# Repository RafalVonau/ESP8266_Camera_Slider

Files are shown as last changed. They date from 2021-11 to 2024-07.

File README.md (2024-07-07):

# Camera slider on ESP8266

## Info

This repository contains the software for my ESP8266 based Camera slider.

Features:
- No collision-detection!!
- WWW page interface ( http://slider.local ),
- Simple commands over TCP (port 2500),
   from linux:
      netcat slider.local 2500
- Simple commands over HTTP POST ( http://slider.local/post ),
- Set mottor current and microsteps per step by a command (software),
- Optional endstop switch for homing.

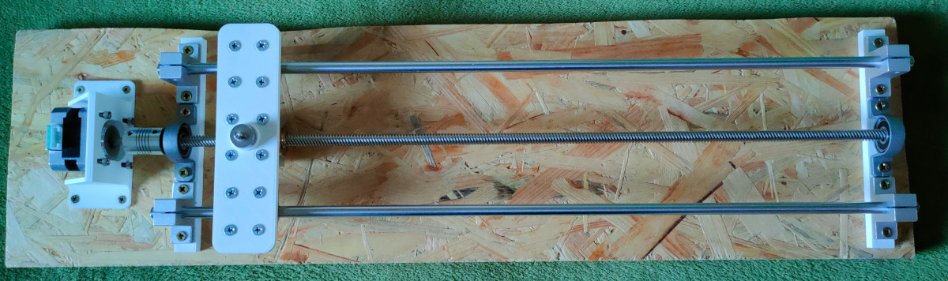
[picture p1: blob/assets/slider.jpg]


# Mechanical parts needed:
* 3D printed pars,
* 1 x T8 Trapezoidal Lead Screw L=500mm,
* 1 x T8 Brass Nut,
* 2 x KP08 Bore Ball Bearing Pillow Block Mounted Support 8mm,
* 2 x 8mm Inner Dia L=34.5mm SCS8UU Linear Bearing,
* 2 x Aluminum 8mm Innner Dia 42x32x11mm SK8 Linear Rod Rail Support Guide Shaft Bearing
* 2 x Linear Shaft Optical Axis 8mm L=500mm,
* 4 x SK8 Linear Rod Rail Shaft,
* 1 x T8 Nut Conversion Seat,
* screws

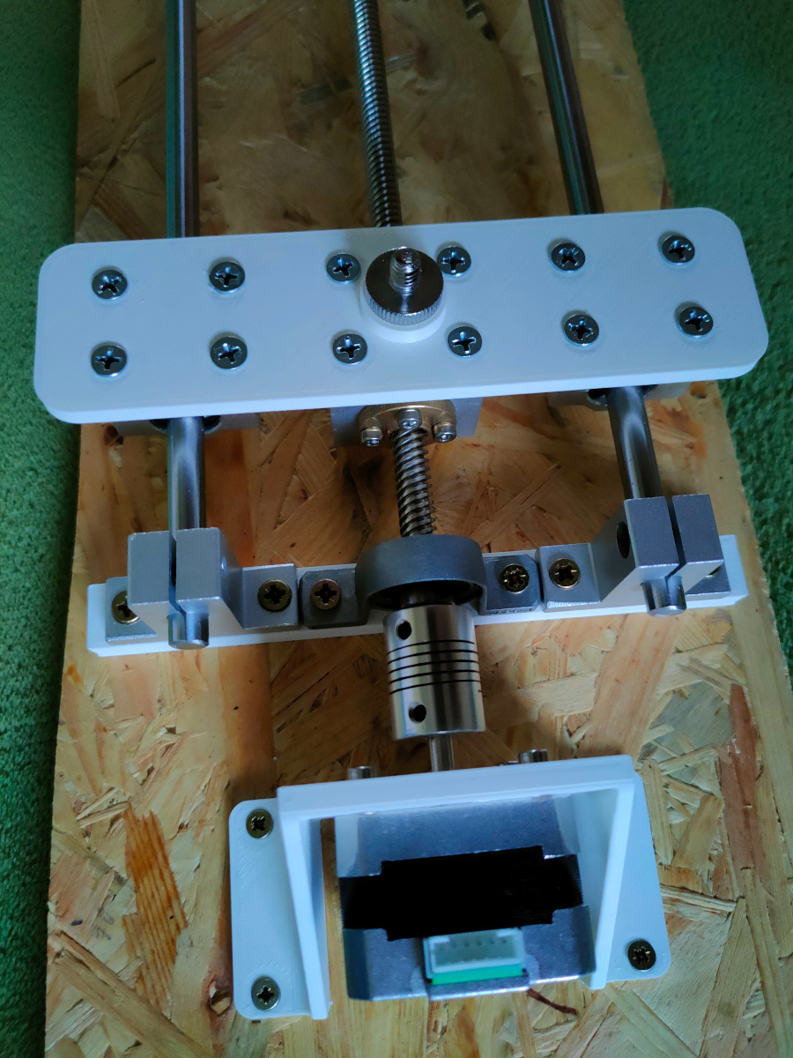
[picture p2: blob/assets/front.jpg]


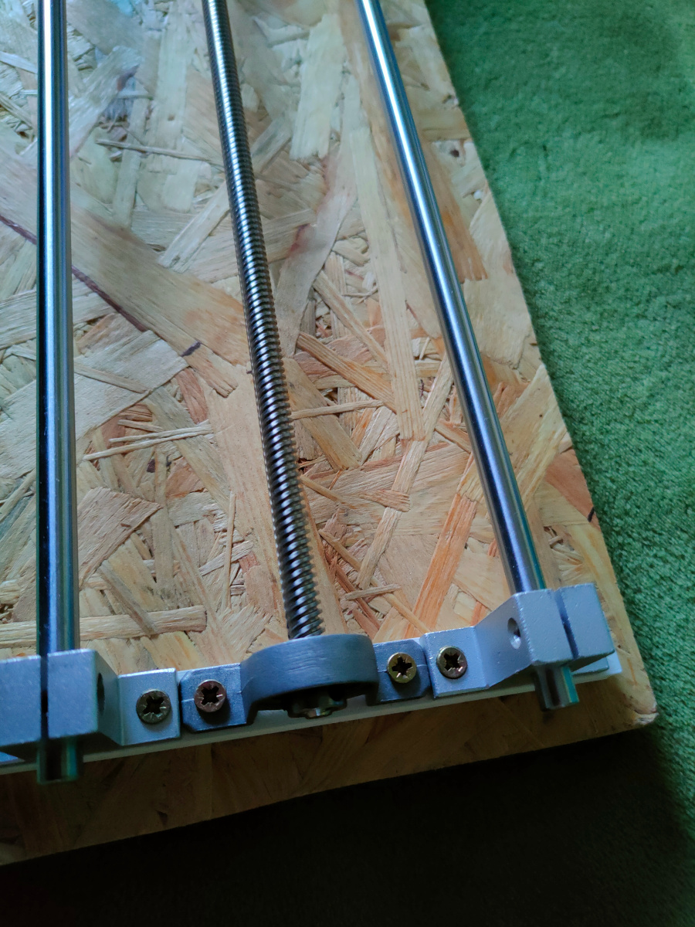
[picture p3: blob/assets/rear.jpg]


# Electrical parts needed:
* ESP8266 (bare ESP8266 module or D1 mini),
* DC/DC converter 12V to 3.3V,
* 1 x TMC2208,
* 1 x Stepper motor Nema 17,
* wires,
* connectors,
* [1 x Limit Switch Endstop for Creality CR-10 10S Ender 3] - OPTIONAL

# D1 mini CONNECTIONS
* STEP      - GPIO14 (D5)
* DIR1      - GPIO13 (D7)
* MOTTOR EN - GPIO2  (D4)
* RX        - TMC2208 single wire UART (1kohm from RX to TX)
* TX        - TMC2208 single wire UART (1kohm from RX to TX)
* ENDSTOP   - GPIO4  (D2)  - OPTIONAL
# Wiring

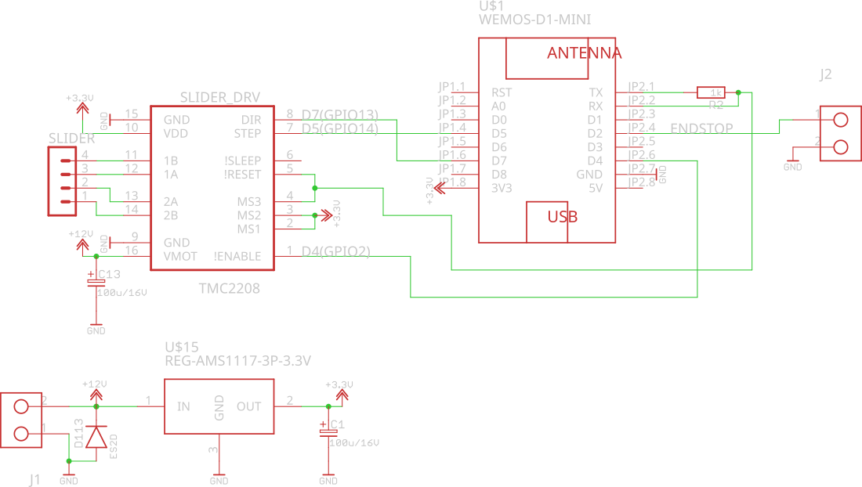
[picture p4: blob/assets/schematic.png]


# Software architecture

The ESP8266 generates STEP and DIR signals to the TMC2208 chip for motor movement. The UART connection allows you to program the TMC2208 chip registers so you can easily change the current and the number of micro steps per step without having to turn a potentiometer or change jumpers. 

STEP signal is generated using Timer1 (for performance reasons the interrupt control was taken from this timer and it was set to AUTORELOAD mode) and because Timer1 is used in servo/pwm(analogWrite)/tone/waveform functions these functions can't be used in this code. 

Commands are received on the fly from TCP channels (port 2500) and the WWW page (POST) and then passed to the command queue. The movement commands are passed to a separate queue so that sequences of movements can be queued. When the move is completed, the next command from the move queue is taken, and so on.

# Building

Uncomment and modify Wifi client settings in secrets.h file:
* #define WIFI_SSID                "Slider"
* #define WIFI_PASS                "SliderPass"

The project uses platformio build environment. 
[PlatformIO](https://platformio.org/) - Professional collaborative platform for embedded development.

* install PlatformIO
* enter project directory
* connect ESP8266 to PC computer over USB to serial cable.
* type in terminal:
  platformio run -t upload

You can also use IDE to build this project on Linux/Windows/Mac. My fvorite ones:
* [Code](https://code.visualstudio.com/) 
* [Atom](https://atom.io/)

# Commands
EM  - enable mottors,

Movement in revolutions:\
M   - absolute move in motor revolutions (M,duration [ms],start_rev,target_rev),\
MR  - relative move in motor revolutions (MR,duration [ms],delta rev),\
MH  - move to home (endstop switch is required),

Movement in microsteps:\
GT  - absolute move in microsteps (GT,duration [ms],start_microstep,target_microstep)\
GTR - relative move in microsteps (GTR,duration [ms],delta microsteps)\
GTH - move to home (endstop switch is required),\
UM  - unconditional relative move in microsteps WARNING: do not check limits. (UM,duration [ms],delta microsteps)

STP - STOP move,

Parameters set:\
G90 - Set this possition as zero point,\
C   - set motor current in [mA],\
S   - set microsteps per step,

STATUS:\
XX  - print status,

Examples:

set mottor curent to 400mA:

C,400

Set 32 misrosteps per step:

S,32

Move from revolution 1 to 45 in 30000 miliseconds:

M,30000,1,45

Move 1 revolution in backward direction in 2 seconds:

MR,2000,1

Stop move:

STP

Enjoy :-)

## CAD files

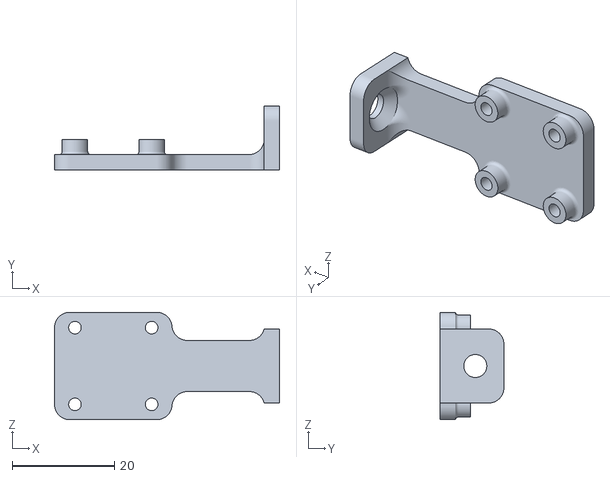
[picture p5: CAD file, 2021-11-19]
PartsTo3DPrint/slider_endstop.stl
44.0 x 12.5 x 21.0

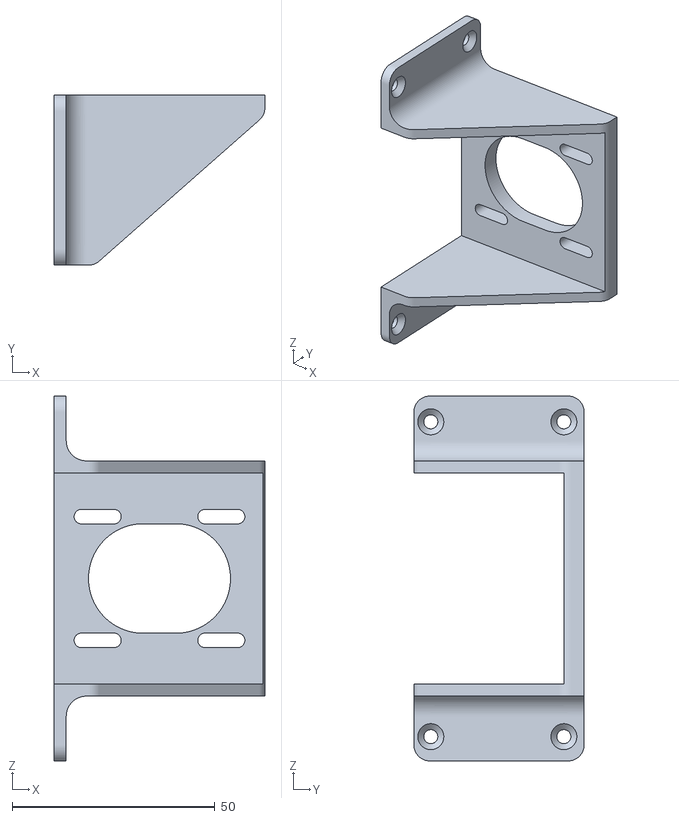
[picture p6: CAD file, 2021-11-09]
PartsTo3DPrint/slider_motor.stl
52.0 x 42.0 x 90.0

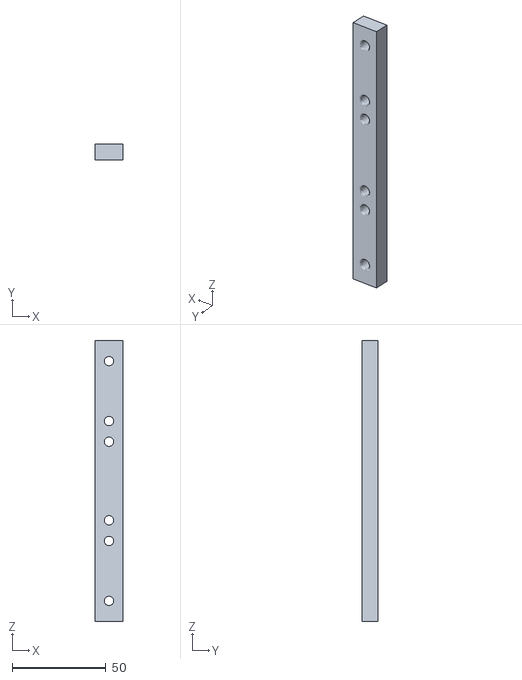
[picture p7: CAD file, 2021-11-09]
PartsTo3DPrint/slider_spacer.stl
15.0 x 8.50 x 150.0

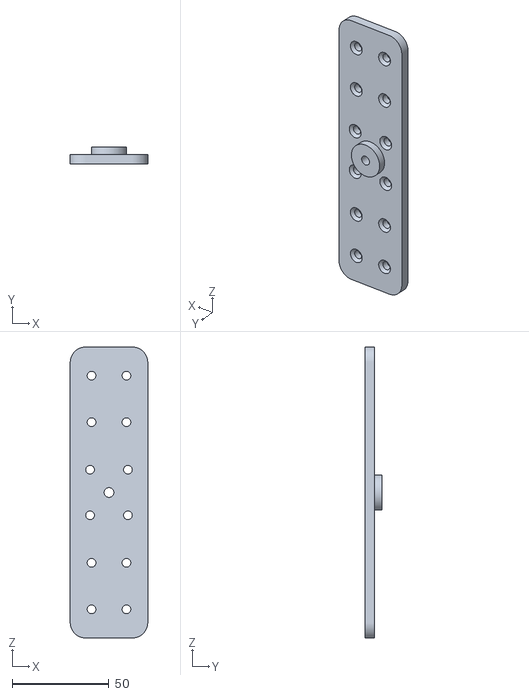
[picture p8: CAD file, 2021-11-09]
PartsTo3DPrint/slider_holder.stl
40.0 x 9.00 x 150.0

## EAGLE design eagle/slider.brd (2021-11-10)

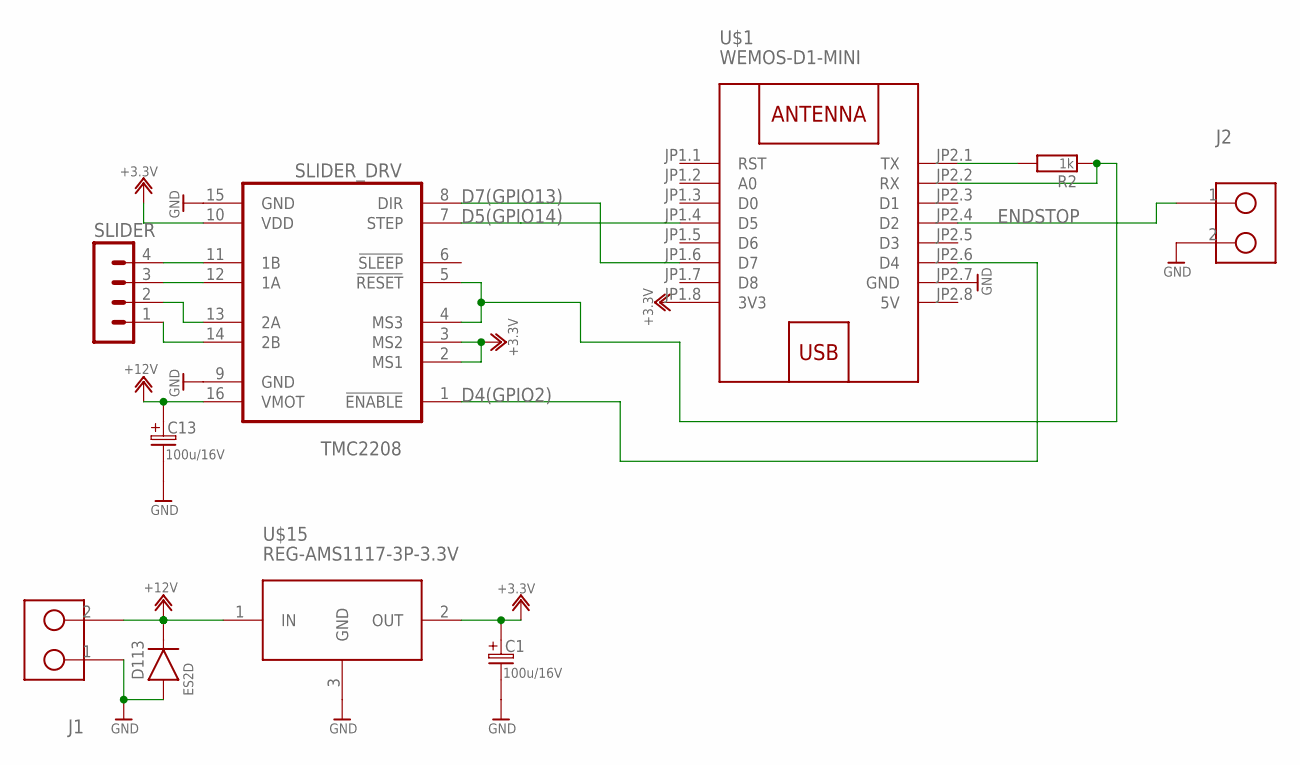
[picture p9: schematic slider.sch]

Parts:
C1, C13: 100u/16V; ES-3,5/8
D113: ES2D; SMB
J1, J2: GMKDS-2; GMKDS1,5
R2: 1k; 0805
SLIDER: MA04-1
SLIDER_DRV: TMC2208; POLOLULU2128
U$1: WEMOS-D1-MINI
U$15: REG-AMS1117-3P-3.3V; REG-AMS1117-3P

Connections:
5V: U$1.JP2.8 (5V)
+3.3V: C1.1, SLIDER_DRV.2 (MS1), SLIDER_DRV.3 (MS2), SLIDER_DRV.10 (VDD), U$1.JP1.8 (3V3), U$15.2 (OUT)
+12V: C13.1, D113.2 (K), J1.2, SLIDER_DRV.16 (VMOT), U$15.1 (IN)
D4(GPIO2): SLIDER_DRV.1 (!ENABLE), U$1.JP2.6 (D4)
D5(GPIO14): SLIDER_DRV.7 (STEP), U$1.JP1.4 (D5)
D7(GPIO13): SLIDER_DRV.8 (DIR), U$1.JP1.6 (D7)
ENDSTOP: J2.1, U$1.JP2.4 (D2)
GND: C1.2, C13.2, D113.1 (A), J1.1, J2.2, SLIDER_DRV.9 (GND), SLIDER_DRV.15 (GND), U$1.JP2.7 (GND), U$15.3 (GND)
unnamed: R2.2, U$1.JP2.1 (TX)
unnamed: R2.1, SLIDER_DRV.4 (MS3), SLIDER_DRV.5 (!RESET), U$1.JP2.2 (RX)
unnamed: SLIDER.4, SLIDER_DRV.11 (1B)
unnamed: SLIDER.3, SLIDER_DRV.12 (1A)
unnamed: SLIDER.2, SLIDER_DRV.13 (2A)
unnamed: SLIDER.1, SLIDER_DRV.14 (2B)

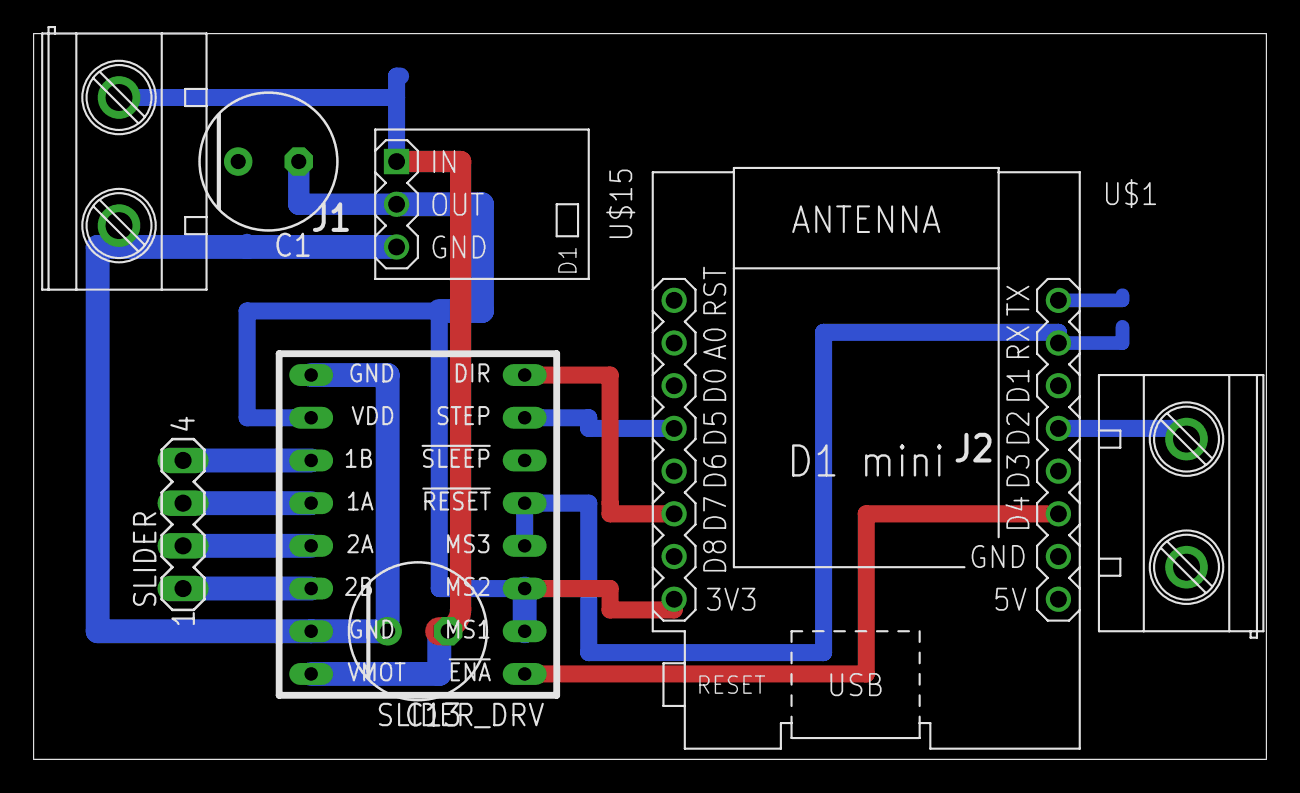
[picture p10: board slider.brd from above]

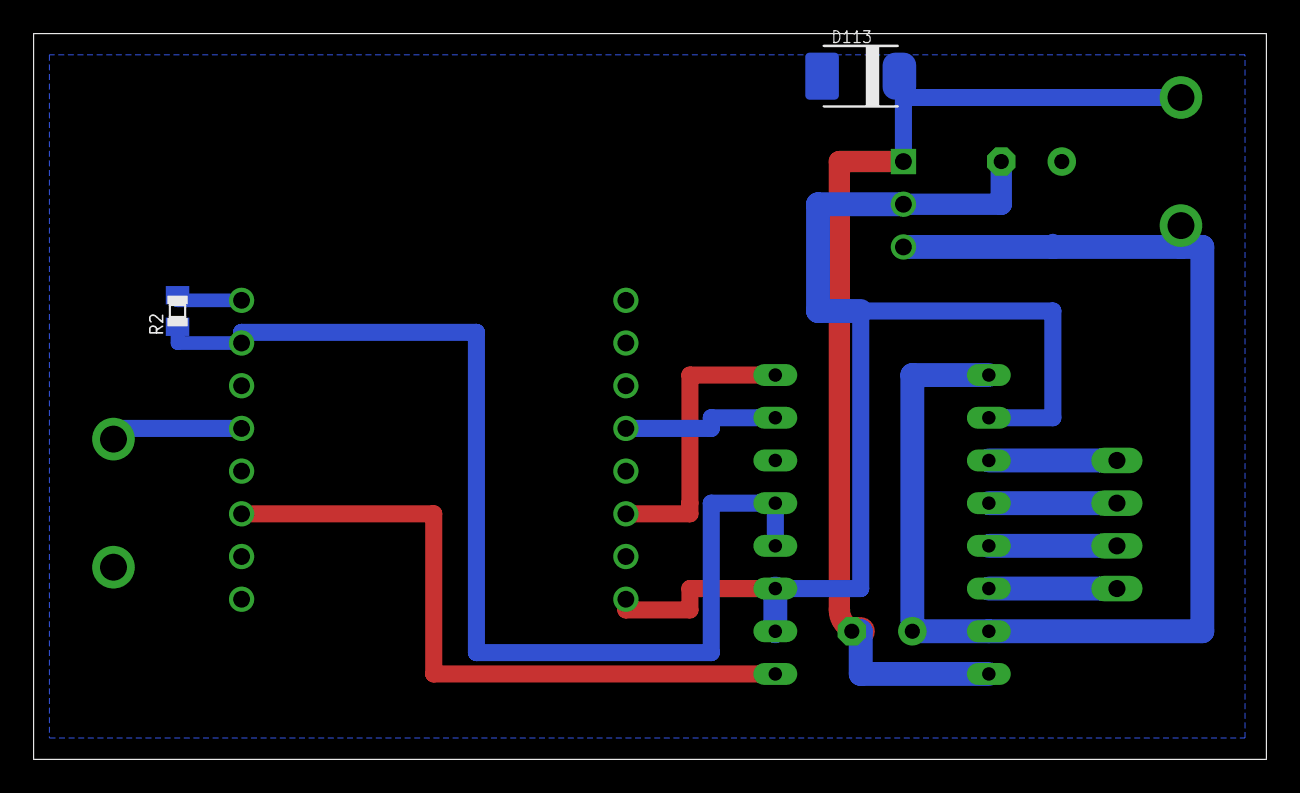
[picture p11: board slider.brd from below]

Board: 2 copper layers, 73.3 x 43.2 mm, 10 parts (2 on the bottom side), 13 nets.

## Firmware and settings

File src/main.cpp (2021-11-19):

#include <ESP8266WiFi.h>
extern "C" {
	#include <osapi.h>
	#include <os_type.h>
}
#include <ArduinoOTA.h>
#include <DNSServer.h>
#include "Motion1D.h"
#include <TMCStepper.h>
#include "NetworkCommand.h"
#include "HTTPCommand.h"
#include "UdpLogger.h"

/* SWITCHES */
#define HOSTNAME                 "slider"
#define NPORT                    (2500)

#define MAX_DIST_MOTTOR (45)

// PIN definition
#define step1        14
#define dir1         13
#define enableMotor  2
#define z_endstop    4


#define SERIAL_PORT Serial    // TMC2208/TMC2224 HardwareSerial port
#define R_SENSE     0.11      // SilentStepStick series use 0.11     Watterott TMC5160 uses 0.075


#ifdef DEBUG_ENABLED
UdpLoggerClass     UdpLogger;
#endif
DNSServer          dnsServer;
class WiFiManager {
	public:
	WiFiManager() {}
	void autoConnect(String x) {
		WiFi.softAP("SliderAP");
		dnsServer.start(53, "*", WiFi.softAPIP());
	}
};
#include "secrets.h"

/* Global variables */
TMC2208Stepper driver = TMC2208Stepper(&SERIAL_PORT, R_SENSE); // Hardware Serial0
Motion1D          *m1d;
CommandDB         CmdDB;
NetworkCommand    *NCmd;
HTTPCommand       *HCmd;
volatile int ota_in_progress = 0;
static int current_microsteps = 256;

static void makeCmdInterface();

/*!
 * \brief Setup.
 * 1. Configure gpio.
 * 2. Connect to WiFi.
 * 3. Setup OTA.
 * 4. Register available commands.
 * 5. Configure TMC2208.
 * 6. Create Motion1D controller.
 */
void setup()
{
	/* Setup pins */
	Serial.begin(115200);
	pinMode(enableMotor, OUTPUT);
	pinMode(step1, OUTPUT);
	pinMode(dir1, OUTPUT);
	digitalWrite(enableMotor, HIGH);
#ifdef z_endstop
	pinMode(z_endstop, INPUT_PULLUP);
#endif	
	/* Connect to WiFi */
	detect_network();
#ifdef DEBUG_ENABLED
	UdpLogger.init(12345, "slider: ");
	//UdpLogger.WriteStartMessage();
#endif
	pdebug("WIFI::IP address: %s\n", WiFi.localIP().toString().c_str());
	/* Setup OTA */
	ArduinoOTA.setHostname(HOSTNAME);
	ArduinoOTA.onStart([]() {
		ota_in_progress = 1;
	});
	ArduinoOTA.begin();
	
	makeCmdInterface();
	
	/* Setup driver */
	digitalWrite(enableMotor, LOW);    // Enable driver in hardware
	driver.begin();
	driver.pdn_disable(true);          // Use PDN/UART pin for communication
	driver.I_scale_analog(false);      // Use internal voltage reference
	driver.rms_current(300);           // Set motor RMS current
	driver.mstep_reg_select(1);        // necessary for TMC2208 to set microstep register with UART
	driver.microsteps(16);
	current_microsteps = 16;
	driver.toff(5);                    // Enables driver in software
	//  driver.en_pwm_mode(true);      // Enable stealthChop
	driver.pwm_autoscale(true);        // Needed for stealthChop
	m1d = new Motion1D(step1, dir1, enableMotor);
	pdebug("Setup done :-)\n");
}
//====================================================================================

/*!
 * \brief MAIN loop.
 * 1. Handle OTA.
 * 2. Handle CMD queue.
 * 3. Handle motion loop.
 */
void loop()
{
	/* Handle OTA */
	ArduinoOTA.handle();
	if (ota_in_progress) return;

	/* Execute command from queue */
	if ( m1d->loop() ) {
		CmdDB.loop();
	} else {
		CmdDB.loopMotion();
		CmdDB.loop();
	}
}
//====================================================================================

/*!
 * \brief Global position estimation.
 */
static int g_pos_x = 0;


#define MAX_DIST_MOTTOR (45)

/*!
 * \brief Move to revolution command (absolute move).
 */
static void stepperMoveAbsoluteRev(CommandQueueItem *c)
{
	int d        = c->m_arg0;
	int newS     = c->m_arg1;
	int newE     = c->m_arg2;
	int duration, aX, dX;
	int speed    = 6000;

	if ((c->m_arg_mask & 7) != 7) {
		c->sendError();
		return;
	}
	
	/* Limit move distance */
	if (newS > MAX_DIST_MOTTOR) newS = MAX_DIST_MOTTOR;
	if (newS < 0) newS = 0;
	if (newE > MAX_DIST_MOTTOR) newE = MAX_DIST_MOTTOR;
	if (newE < 0) newE = 0;
	
	/* Convert to microsteps */
	newS*=(200 * current_microsteps);
	newE*=(200 * current_microsteps);

	dX = newS - g_pos_x;
	if (dX < 0) aX = -dX; else aX = dX;

	/* Calculate duration in [ms] */
	if (aX) {
		duration = (aX * 1000)/speed;
		m1d->goTo(duration, dX);
	}
	g_pos_x = newS;

	dX = newE - g_pos_x;
	if (dX < 0) aX = -dX; else aX = dX;
	if (aX) {
		m1d->goTo(d, dX);
	}
	g_pos_x = newE;
	c->sendAck();
}
//====================================================================================

/*!
 * \brief Move relative command (in revolution).
 */
static void stepperMoveRelativeRev(CommandQueueItem *c)
{
	int d        = c->m_arg0;
	int newS     = g_pos_x + (c->m_arg1 * 200 * current_microsteps);
	int aX, dX, mm = MAX_DIST_MOTTOR * 200 * current_microsteps;

	if ((c->m_arg_mask & 3) != 3) {
		c->sendError();
		return;
	}
	/* Limit move distance */
	if (newS > mm) newS = mm;
	if (newS < 0) newS = 0;
	
	dX = newS - g_pos_x;
	if (dX < 0) aX = -dX; else aX = dX;
	if (aX) {
		m1d->goTo(d, dX);
	}
	g_pos_x = newS;
	c->sendAck();
}
//====================================================================================

/*!
 * \brief Move to position command (absolute move).
 */
static void stepperMoveAbsolute(CommandQueueItem *c)
{
	int d        = c->m_arg0;
	int newS     = c->m_arg1;
	int newE     = c->m_arg2;
	int duration, aX, dX;
	int speed    = 3000;
	int mm = MAX_DIST_MOTTOR * 200 * current_microsteps;

	if ((c->m_arg_mask & 7) != 7) {
		c->sendError();
		return;
	}
	
	/* Limit move distance */
	if (newS > mm) newS = mm;
	if (newS < 0) newS = 0;
	if (newE > mm) newE = mm;
	if (newE < 0) newE = 0;
	
	dX = newS - g_pos_x;
	if (dX < 0) aX = -dX; else aX = dX;

	/* Calculate duration in [ms] */
	if (aX) {
		duration = (aX * 1000)/speed;
		m1d->goTo(duration, dX);
	}
	g_pos_x = newS;

	dX = newE - g_pos_x;
	if (dX < 0) aX = -dX; else aX = dX;
	if (aX) {
		m1d->goTo(d, dX);
	}
	g_pos_x = newE;
	c->sendAck();
}
//====================================================================================

/*!
 * \brief Move relative command (in microsteps).
 */
static void stepperMoveRelative(CommandQueueItem *c)
{
	int d        = c->m_arg0;
	int newS     = g_pos_x + c->m_arg1;
	int aX, dX, mm = MAX_DIST_MOTTOR * 200 * current_microsteps;

	if ((c->m_arg_mask & 3) != 3) {
		c->sendError();
		return;
	}
	/* Limit move distance */
	if (newS > mm) newS = mm;
	if (newS < 0) newS = 0;
	
	dX = newS - g_pos_x;
	if (dX < 0) aX = -dX; else aX = dX;
	if (aX) {
		m1d->goTo(d, dX);
	}
	g_pos_x = newS;
	c->sendAck();
}
//====================================================================================

/*!
 * \brief Move uncondicional - do not check limits (in microsteps).
 */
static void stepperMoveUncondicional(CommandQueueItem *c)
{
	int d        = c->m_arg0;
	int newS     = g_pos_x + c->m_arg1;
	int aX, dX;

	if ((c->m_arg_mask & 3) != 3) {
		c->sendError();
		return;
	}
	dX = newS - g_pos_x;
	if (dX < 0) aX = -dX; else aX = dX;
	if (aX) {
		m1d->goTo(d, dX);
	}
	g_pos_x = newS;
	c->sendAck();
}
//====================================================================================

/*!
 * \brief STOP movement.
 */
static void stepperMoveStop(CommandQueueItem *c)
{
	m1d->stop();
	g_pos_x = x_pos;
	c->sendAck();
}
//====================================================================================

/*!
 * \brief Set zero.
 */
void cmdG90(CommandQueueItem *c)
{
	m1d->stop();
	g_pos_x  = 0;
	x_pos    = 0;
	x_target = 0;
	c->sendAck();
}
//====================================================================================

/*!
 * \brief CmdHome (detect home).
 */
void cmdHome(CommandQueueItem *c)
{
#ifdef z_endstop
	/* Execute movement */
	int newS     = g_pos_x - ((MAX_DIST_MOTTOR + 1) * 200 * current_microsteps);
	int duration, aX, dX;
	int speed    = 6000;

	dX = newS - g_pos_x;
	if (dX < 0) aX = -dX; else aX = dX;
	/* Calculate duration in [ms] */
	if (aX) {
		duration = (aX * 1000)/speed;
		m1d->goTo(duration, dX);
	}
	g_pos_x = newS;
	/* Wait for motion to end */
	while ( m1d->isInMotion() ) {
		m1d->loop();
		CmdDB.loop();
		if ((digitalRead(z_endstop)) == 0) {
			cmdG90(c);
			return;
		}
		yield();
	}
	c->sendErrorText("Can not find HOME edge!!!");
#else
	/* GoTo 0 */
	int newS     = 0;
	int duration, aX, dX;
	int speed    = 3000;

	dX = newS - g_pos_x;
	if (dX < 0) aX = -dX; else aX = dX;
	/* Calculate duration in [ms] */
	if (aX) {
		duration = (aX * 1000)/speed;
		m1d->goTo(duration, dX);
	}
	g_pos_x = newS;
	c->sendAck();
#endif
}
//====================================================================================


/*!
 * \brief Set mottor current in [mA] command.
 */
static void cmdCurrent(CommandQueueItem *c)
{
	if ((c->m_arg_mask & 1) != 1) {
		c->sendError();
		return;
	}
	driver.rms_current(c->m_arg0);
	c->sendAck();
}
//====================================================================================

/*!
 * \brief Set microsteps per step command.
 */
static void cmdSteps(CommandQueueItem *c)
{
	if ((c->m_arg_mask & 1) != 1) {
		c->sendError();
		return;
	}
	driver.mstep_reg_select(1);        // necessary for TMC2208 to set microstep register with UART
	driver.microsteps(c->m_arg0);
	current_microsteps = c->m_arg0;
	c->sendAck();
}
//====================================================================================

/*!
 * \brief Enable/Disable mottors command..
 */
static void enableMotors(CommandQueueItem *c)
{
	int value = -1, cmd = -1;

	if (c->m_arg_mask & 1) cmd = c->m_arg0;
	if (c->m_arg_mask & 2) value = c->m_arg1;

	if ((cmd != -1) && (value == -1)) {
		switch (cmd) {
			case 0: {m1d->motorsOff();c->sendAck();}break;
			case 1: {m1d->motorsOn();c->sendAck();}break;
			default: c->sendError(); break;
		}
	}
	if ((cmd != -1) && (value != -1)) {
		switch (value) {
			case 0: {m1d->motorsOff();c->sendAck();}break;
			case 1: {m1d->motorsOn();c->sendAck();}break;
			default: c->sendError(); break;
		}
	}
}
//====================================================================================

static void unrecognized(const char *command, Command *c) {c->print("!8 Err: Unknown command\r\n");}

/*!
 * \brief Fill commands database.
 */
static void makeCmdInterface()
{
	CmdDB.addCommand("v",[](CommandQueueItem *c) {
		c->print("Slider-Firmware V1.0\r\n");
	});
	CmdDB.addCommand("EM" ,enableMotors);
	/* Motion commands */
	CmdDB.addCommand("M"  ,stepperMoveAbsoluteRev, true);
	CmdDB.addCommand("MR" ,stepperMoveRelativeRev, true);
	CmdDB.addCommand("MH", cmdHome, true);
	CmdDB.addCommand("GT" ,stepperMoveAbsolute, true);
	CmdDB.addCommand("GTR",stepperMoveRelative, true);
	CmdDB.addCommand("GTH",cmdHome, true);
	CmdDB.addCommand("UM" ,stepperMoveUncondicional, true);
	CmdDB.addCommand("STP",stepperMoveStop);
	/* Parameters */
	CmdDB.addCommand("G90",cmdG90, true);
	CmdDB.addCommand("C"  ,cmdCurrent, true);
	CmdDB.addCommand("S"  ,cmdSteps, true);
	/* Status */
	CmdDB.addCommand("XX" ,[](CommandQueueItem *c){m1d->printStat(c);});
	CmdDB.setDefaultHandler(unrecognized); // Handler for command that isn't matched (says "What?")

	NCmd = new NetworkCommand(&CmdDB, NPORT);
	HCmd = new HTTPCommand(&CmdDB);
}
//====================================================================================

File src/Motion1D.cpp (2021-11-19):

/*
 * One axis (1D) motion class for ESP8266 (simple constant speed no RAMP motion controll).
 *
 * Author: Rafal Vonau <rafal.vonau@gmail.com>
 *
 * This program is free software; you can redistribute it and/or modify
 * it under the terms of the GNU General Public License version 3 as
 * published by the Free Software Foundation.
 */
extern "C" {
	#include <osapi.h>
	#include <os_type.h>
}
#include "Motion1D.h"
#include "esp8266_gpio_direct.h"
#include "core_esp8266_waveform.h"
#include "ramp.h"

#define TIMER1_DIVIDE_BY_1              0x0000
#define TIMER1_DIVIDE_BY_16             0x0004
#define TIMER1_ENABLE_TIMER             0x0080
#define TIMER1_AUTORELOAD               (1u<<6)

#define MIN_PERIOD                      (4000)

static volatile int        int_active       = 0;   /*!< Timer1 interrupt is active (Timer1 is running).   */
static volatile int        in_motion        = 0;   /*!< We are in motion.                                 */

/* X */
static uint16_t            x_gpio_mask      = 0;   /*!< GPIO mask for STEP pin.                           */
static volatile uint32_t   x_hperiod        = 0;   /*!< TIMER1 half period in clock cycles (80MHz clock). */
volatile int               x_target         = 0;   /*!< Target position.                                  */
volatile int               x_pos            = 0;   /*!< Current position.                                 */
static volatile int        x_pulse          = 0;   /*!< STEP pulse phase 0 (level 0), 1 (level 1).        */

#ifdef USE_RAMP
volatile int               x_pos_start      = 0;   /*!< Motion start position.                            */
volatile int               x_pos_middle     = 0;   /*!< Motion middle point.                              */
volatile int               x_ramp_len       = 0;   /*!< Motion ramp length.                               */
volatile int               x_ramp_pos       = 0;   /*!< Current ramp table index.                         */
volatile int               x_ramp_iter      = 0;   /*!< Current iterations.                               */
volatile int               x_ramp_phase     = 0;   /*!< Current ramp phase.                               */
volatile uint32_t          x_target_hperiod = 0;   /*!< Target half period.                               */
volatile int               x_dir            = 0;   /*!< Motion direction.                                 */
#endif



struct timer_regs {
	uint32_t frc1_load;   /* 0x60000600 */
	uint32_t frc1_count;  /* 0x60000604 */
	uint32_t frc1_ctrl;   /* 0x60000608 */
	uint32_t frc1_int;    /* 0x6000060C */
	uint8_t  pad[16];
	uint32_t frc2_load;   /* 0x60000620 */
	uint32_t frc2_count;  /* 0x60000624 */
	uint32_t frc2_ctrl;   /* 0x60000628 */
	uint32_t frc2_int;    /* 0x6000062C */
	uint32_t frc2_alarm;  /* 0x60000630 */
};
static struct timer_regs* timer = (struct timer_regs*)(void*)(0x60000600);

static void motion_intr_handler(void);

//#pragma GCC optimize ("Os")

static inline ICACHE_RAM_ATTR uint32_t GetCycleCount()
{
	uint32_t ccount;
	__asm__ __volatile__("esync; rsr %0,ccount":"=a"(ccount));
	return ccount;
}
//===========================================================================================

/*!
 * \brief Disable Timer1.
 */
static inline ICACHE_RAM_ATTR void motion1D_timer1_disable()
{
	timer->frc1_int &= ~FRC1_INT_CLR_MASK;
	timer->frc1_ctrl = 0;
	ETS_FRC_TIMER1_INTR_ATTACH(motion_intr_handler, NULL);
	TM1_EDGE_INT_ENABLE();
	timer->frc1_int &= ~FRC1_INT_CLR_MASK;
	timer->frc1_ctrl = 0;
	int_active       = 0;
}
//===========================================================================================

/*!
 * \brief Enable Timer1.
 */
static inline ICACHE_RAM_ATTR void motion1D_timer1_enable()
{
	int_active = 1;
	ETS_FRC1_INTR_ENABLE();
	RTC_REG_WRITE(FRC1_LOAD_ADDRESS, x_hperiod);
	timer->frc1_int &= ~FRC1_INT_CLR_MASK;
	timer->frc1_ctrl = TIMER1_DIVIDE_BY_1 | TIMER1_AUTORELOAD | TIMER1_ENABLE_TIMER;
}
//===========================================================================================


void Motion1D::printStat(CommandQueueItem *c)
{
	c->print("now="+String(GetCycleCount()) + "\r\nint_active="+String(int_active)+"\r\nin_motion="+String(in_motion)+"\r\n" + \
		"x_pulse="+String(x_pulse)+ "\r\n" \
		"x_pos="+String(x_pos)+",target = "+String(x_target)+"\r\nOK\r\n");
}
//===========================================================================================



/*!
 * \breif Constructor.
 */
Motion1D::Motion1D(int step1, int dir1, int en_pin)
{
	pinMode(step1, OUTPUT);
	pinMode(dir1, OUTPUT);
	digitalWrite(step1, LOW);
	m_x_dir         = dir1;
	x_gpio_mask     = (1 << step1);
	/* Disable timer */
	motion1D_timer1_disable();
	in_motion       = 0;
	m_en_pin        = en_pin;
	m_motorsEnabled = 0;
	pinMode(en_pin, OUTPUT);
	motorsOff();
#ifdef MOTION_QUEUE_SIZE
	m_motionQWr   = 0;
	m_motionQRd   = 0;
#endif
}
//====================================================================================


void Motion1D::stop()
{
	/* Flush the motion Queue */
#ifdef MOTION_QUEUE_SIZE
	m_motionQWr   = 0;
	m_motionQRd   = 0;
#endif
	/* Stop timer 1 */
	motion1D_timer1_disable();
	x_target = x_pos;
	if (x_pulse) {
		asm volatile ("" : : : "memory");
		gpio_r->out_w1tc = (uint32_t)(x_gpio_mask);
		x_pulse = 0;
	}
}
//====================================================================================

/*!
 * \brief Disable Motors.
 */
void Motion1D::motorsOff()
{
	digitalWrite(m_en_pin, HIGH);
	m_motorsEnabled = 0;
}
//====================================================================================

/*!
 * \brief Enable Motors.
 */
void Motion1D::motorsOn()
{
	digitalWrite(m_en_pin, LOW) ;
	m_motorsEnabled = 1;
}
//====================================================================================

/*!
 * \brief Toggle Motors.
 */
void Motion1D::toggleMotors()
{
	if (m_motorsEnabled) {
		motorsOff();
	} else {
		motorsOn();
	}
}
//====================================================================================
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

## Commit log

2021-11-09 Initial import
    [slider.brd, slider.sch]
2021-11-09 STL and JPEG files
    [slider_holder.stl, slider_mottor.stl, slider_spacer.stl]
2021-11-10 Optional endstop for homming
2021-11-10 Schematic fixups
    [slider.brd, slider.sch]
2021-11-10 endstop stl file
    [slider_endstop.stl]

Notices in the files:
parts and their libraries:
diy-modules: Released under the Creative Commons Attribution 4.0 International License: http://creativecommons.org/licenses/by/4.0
